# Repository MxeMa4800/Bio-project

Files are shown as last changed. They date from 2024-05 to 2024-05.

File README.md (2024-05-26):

# Stegosaurus Project
The goal of this project is to create a moving robot by controlling it with a Central Pattern Generator (CPG) and virtual hormones, which simulate how the nervous system works in living things. To guarantee the robot operates realistically, the project also entails building physical models in SolidWorks and constructing electrical circuits.

## Installation 
In order to ensure a smooth start, this section includes a list of prerequisites and instructions for installing the required hardware and software for the robot project.

### **Prerequisites**

1. Operating System 
   - Windows

      
      

2. Software 
- Arduino IDE (for programming Arduino)

   
   
   

- SolidWorks (for robot design)

    
   
   

 3. Hardware

      <table style="width:100%; border-collapse: collapse;">
      <thead>
         <tr>
            <th style= "text-align:center;">No.</th>
            <th style= "text-align:center;">List</th>
            <th style= "text-align:center;">Image</th>
            <th style= "text-align:center;">Amount (Pcs)</th>
         </tr>
      </thead>
      <tbody>
         <tr>
            <td style= "text-align:center;">1.</td>
            <td style= "text-align:center;">Arduino UNO R4 WIFI</td>
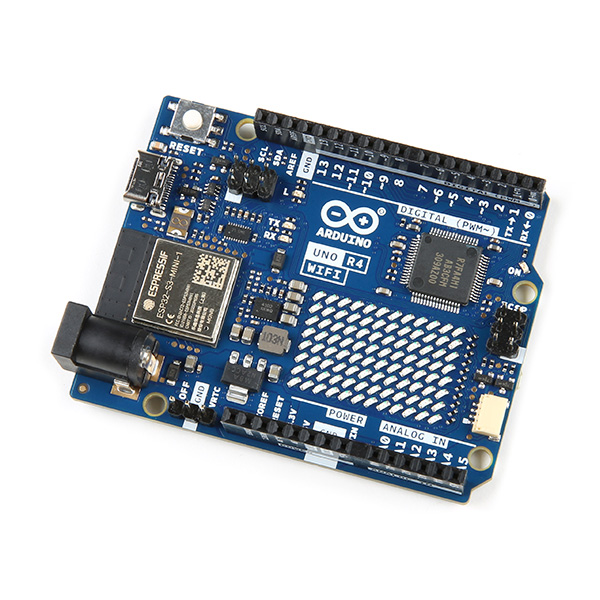
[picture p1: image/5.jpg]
            <td style= "text-align:center;"></td>
            <td style= "text-align:center;">1</td>
         </tr>
         <tr>
            <td style= "text-align:center;">2.</td>
            <td style= "text-align:center;">FE-URT-1</td>
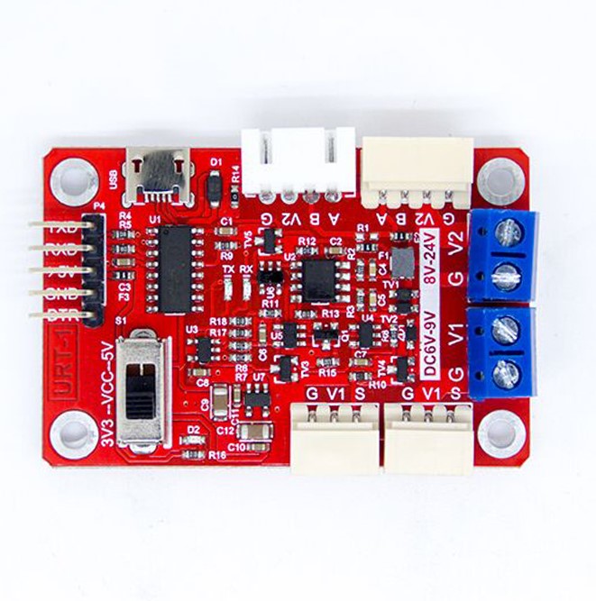
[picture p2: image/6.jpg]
            <td style= "text-align:center;"></td>
            <td style= "text-align:center;">1</td>
         </tr>
         <tr>
            <td style= "text-align:center;">3.</td>
            <td style= "text-align:center;">SCS15</td>
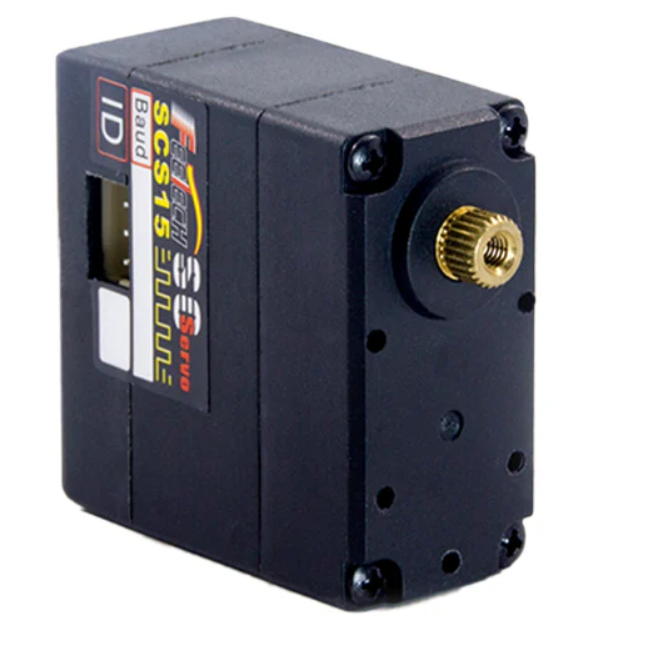
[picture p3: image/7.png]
             <td style= "text-align:center;"></td>
            <td style= "text-align:center;">8</td>
         </tr>
         </tr>
            <td style= "text-align:center;">4.</td>
            <td style= "text-align:center;">Helicox 3000mA</td>
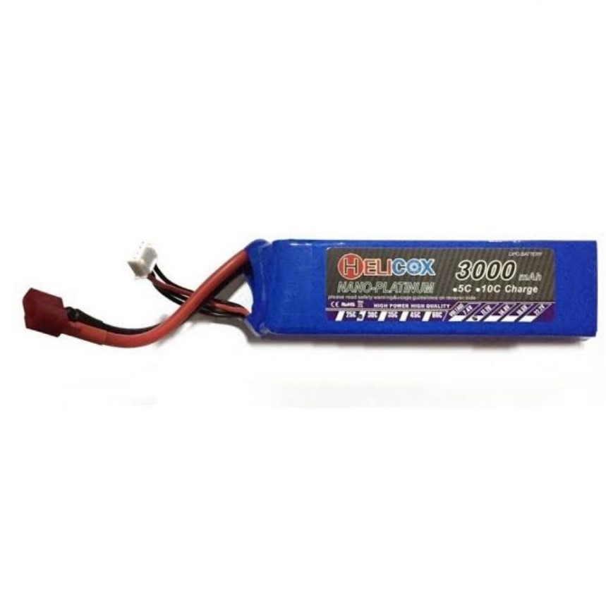
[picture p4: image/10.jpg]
             <td style= "text-align:center;"></td>
            <td style= "text-align:center;"> 1 </td>
         </tr>
         </tr>
            <td style= "text-align:center;">5.</td>
            <td style= "text-align:center;">US-015 Ultrasonic Sensor Module</td>
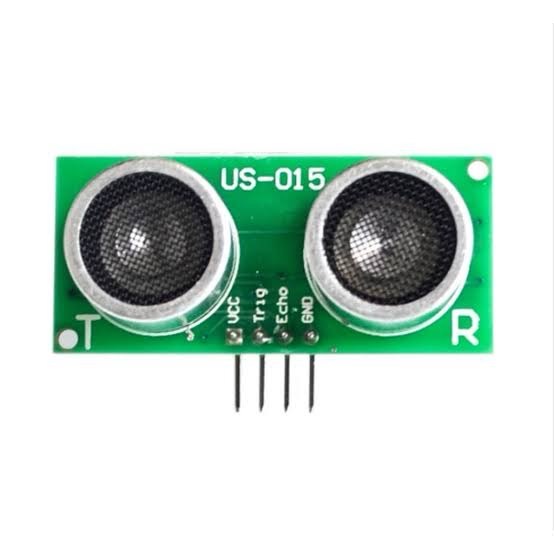
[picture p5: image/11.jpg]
             <td style= "text-align:center;"></td>
            <td style= "text-align:center;"> 2 </td>
         </tr>
          </tr>
            <td style= "text-align:center;">6.</td>
            <td style= "text-align:center;">Vehicle tires</td>
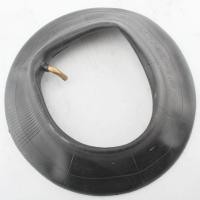
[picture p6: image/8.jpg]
             <td style= "text-align:center;"></td>
            <td style= "text-align:center;"> 1 </td>
         </tr>
      </tbody>
      </table>

### **Software Installation Steps**
1. Install Arduino IDE
- The Arduino IDE can be downloaded and installed from the [Arduino website](https://www.arduino.cc/en/software/).
- Launch the Arduino IDE and add the required libraries, like Math and [SCServo](https://github.com/IS2511/SCServo/blob/master/SCSCL.cpp). 
   
   **Zip file installation for the library**
   - Get the Library from here in a zip file. 

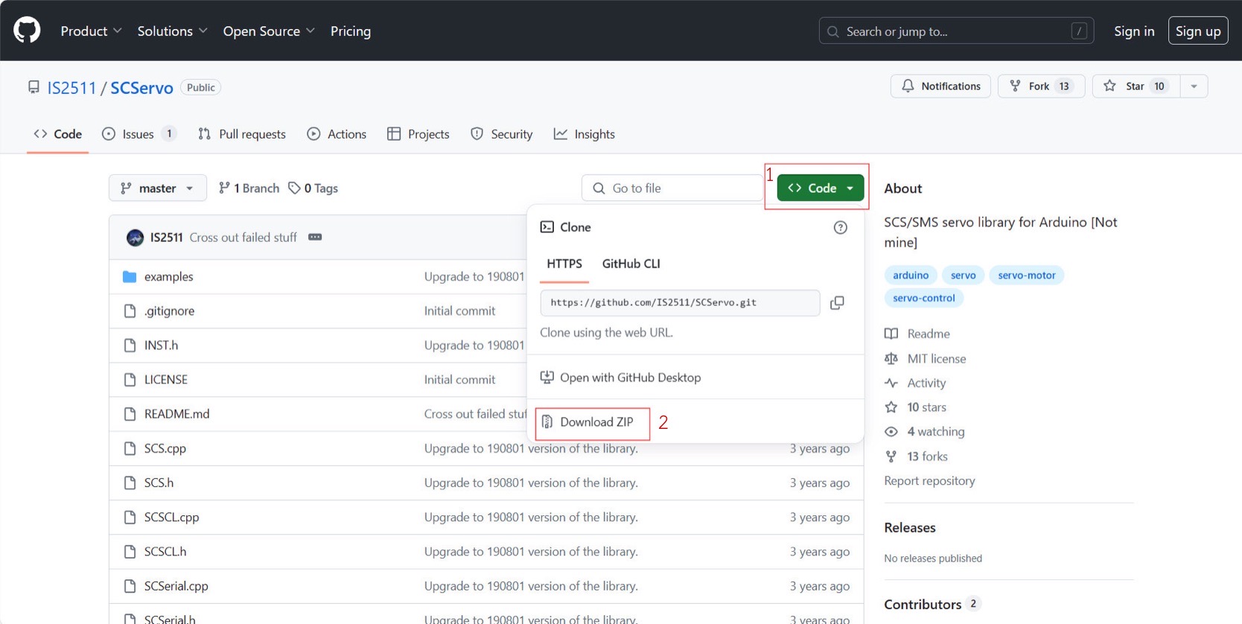
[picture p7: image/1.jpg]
      

   - Open the Arduino IDE program, go to Sketch > Include Library > Add .ZIP Library, then pick the file that you downloaded.

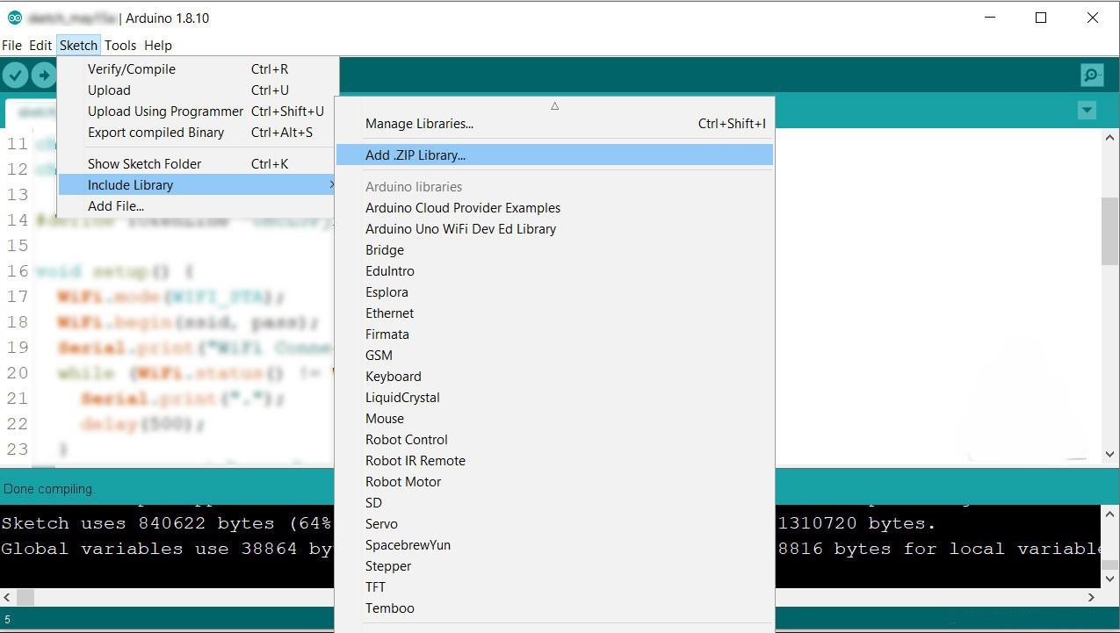
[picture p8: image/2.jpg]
      

    **Installing more Arduino libraries**

     - Open the Arduino IDE program, go to Sketch > Include Library > Manage Libraries.
     
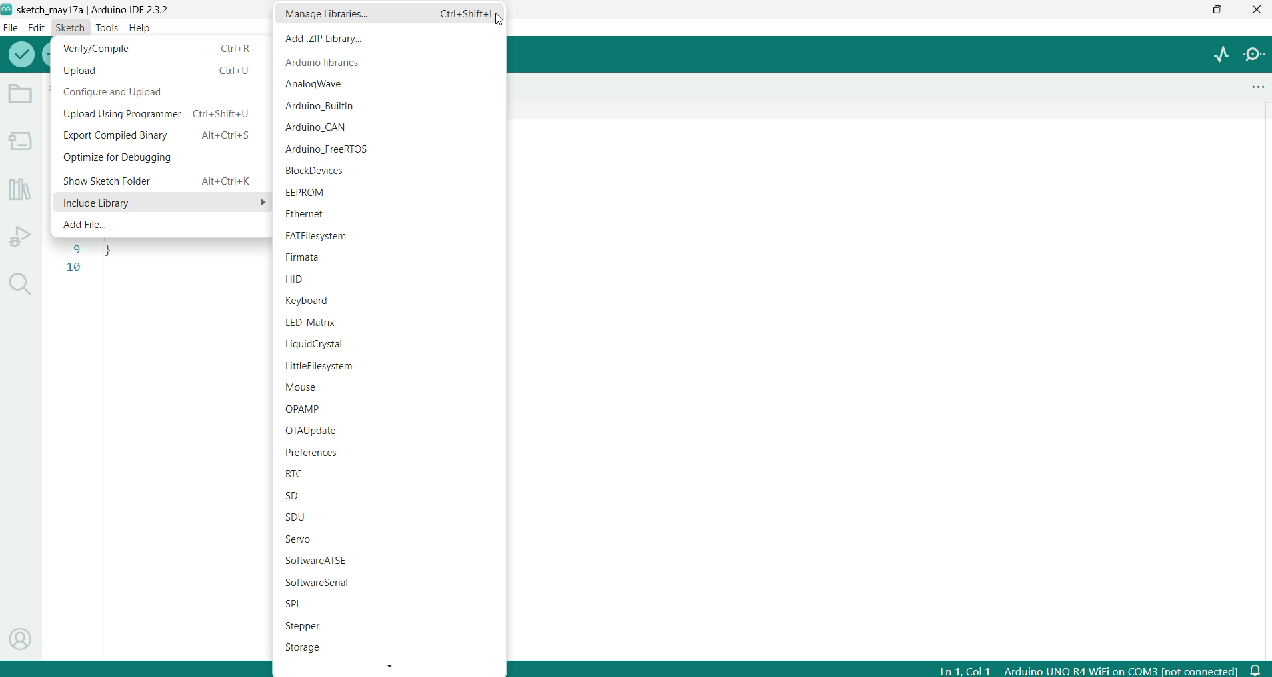
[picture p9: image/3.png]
        

    - In the search box, type the name of the desired library. Click More info to see how to utilize it. Click the Install button in order to install.
      
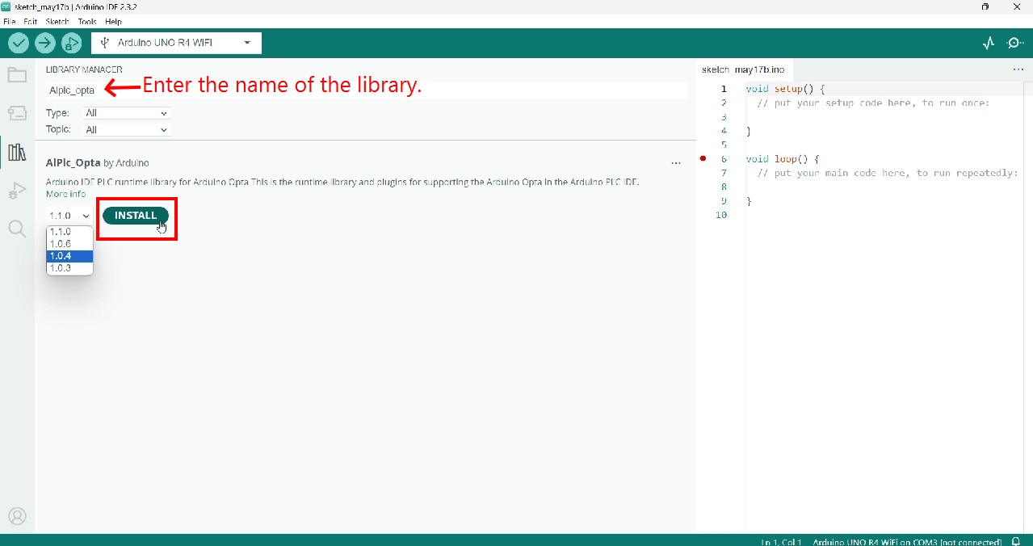
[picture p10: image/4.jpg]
      

2. Install SolidWorks
- SolidWorks can be downloaded and installed from the [SolidWorks official website](https://www.solidworks.com/sw/support/downloads.htm).
- Launch SolidWorks and confirm that all required modules, including Part, Simulation and Electrical, are installed.

### **Hardware Installation Steps**
1. Assemble the Robot Structure
- The robot's primary structure can be constructed using the assembly guide found in the SolidWorks files.
- Place electrical in the designated locations.   
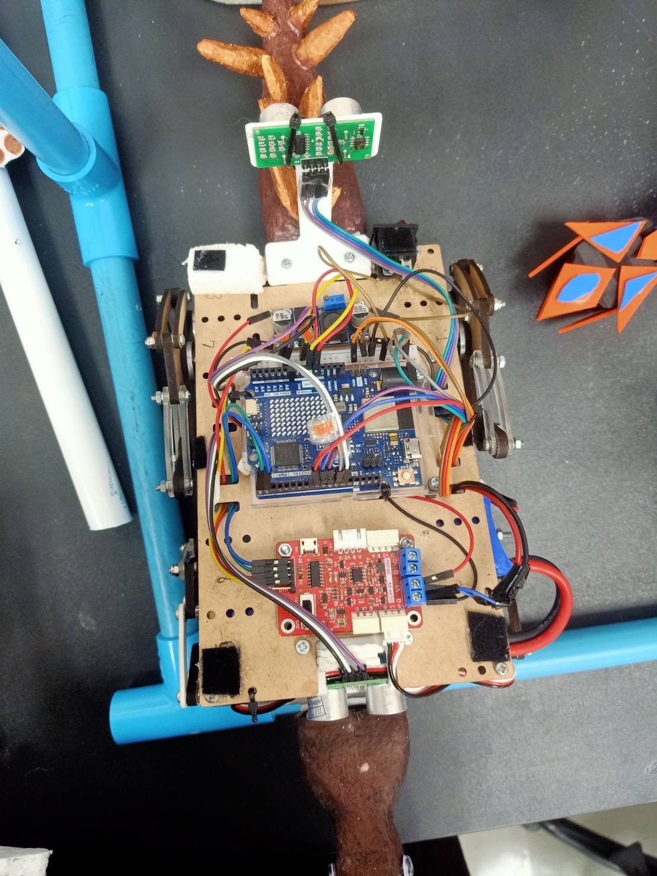
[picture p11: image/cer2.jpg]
   
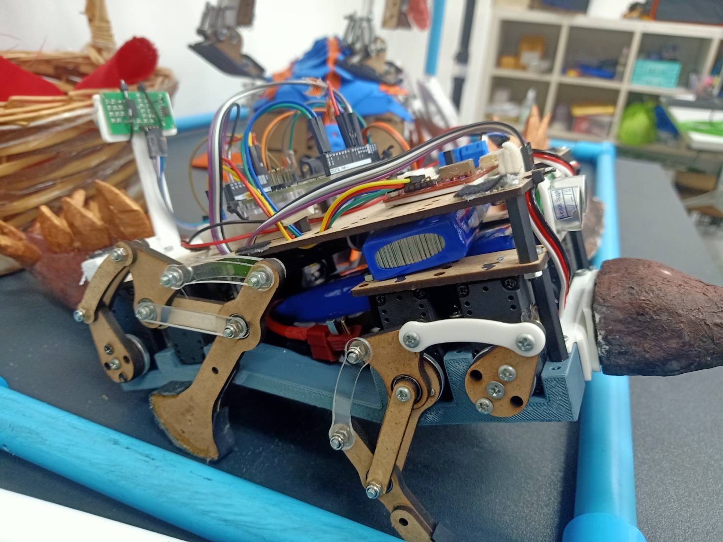
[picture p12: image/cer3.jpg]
   
2. Connect the Electrical Circuit

- Wires between the microcontroller(Arduino uno r4), servo, sensors, and batteries should be installed and connected using the electrical circuit schematic.
- Make sure every connection is safe and secure.

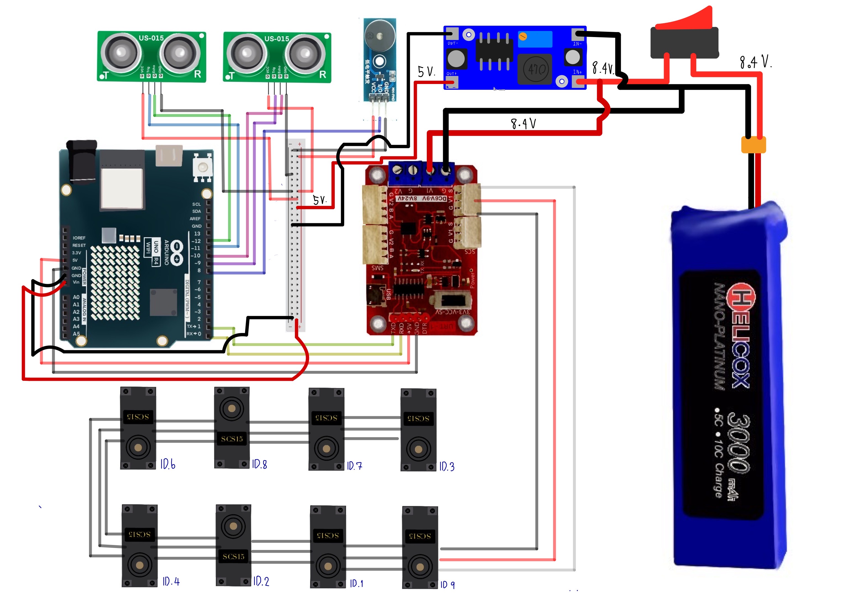
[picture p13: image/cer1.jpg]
   

3. Energy consumption
   - The battery used is a Helicox 3000mA. A single battery can last approximately 1-2 hours,    as can be seen from the following calculations
     
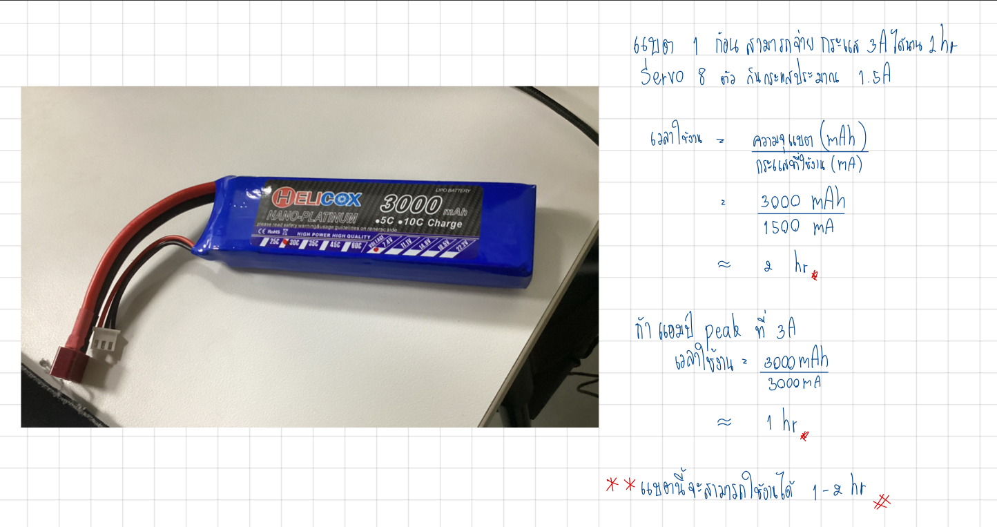
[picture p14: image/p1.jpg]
     
## Robot Design
### **Main Structure**
1. This robot is designed to walk on four legs, with the main materials used being: 

   - PLA+ Filament 

   - Acrylic 2 mm thick 

   - Wooden boards 2.5 mm and 4 mm
     
   ** Replacing the leg material from wood to acrylic might yield better results, but be cautious of material breakage.
   
   Assemble whit out skin
   
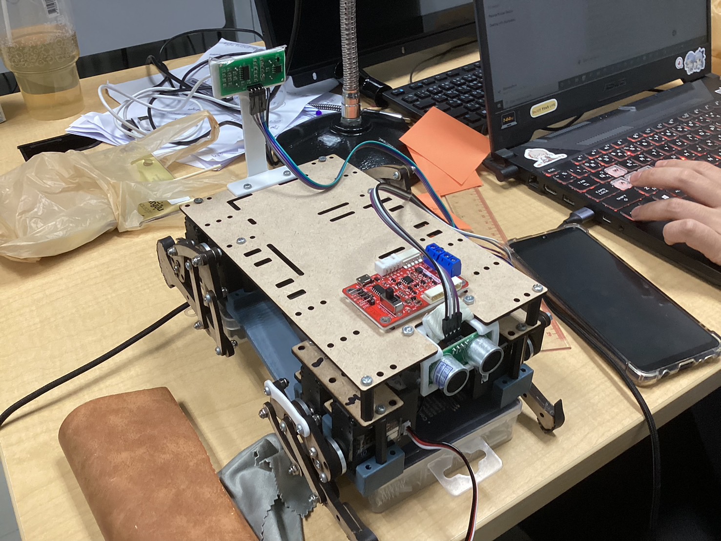
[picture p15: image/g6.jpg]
   
   
   Assemble full skin
   
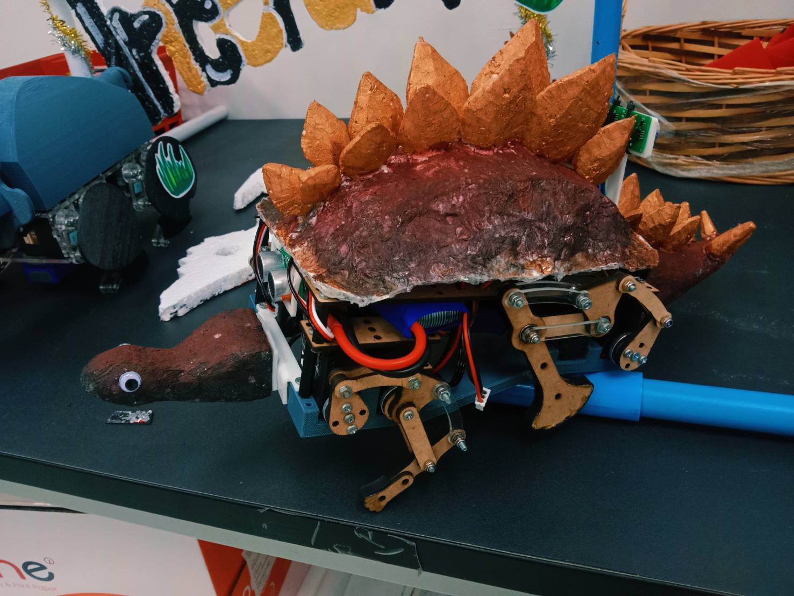
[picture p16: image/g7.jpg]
   

 3. The skeleton of the Stegosaurus has front and hind legs of different sizes. Therefore, the designer made the front and hind legs of different sizes, with a ratio of 1:1.51, but the size difference does not exceed 2 times.
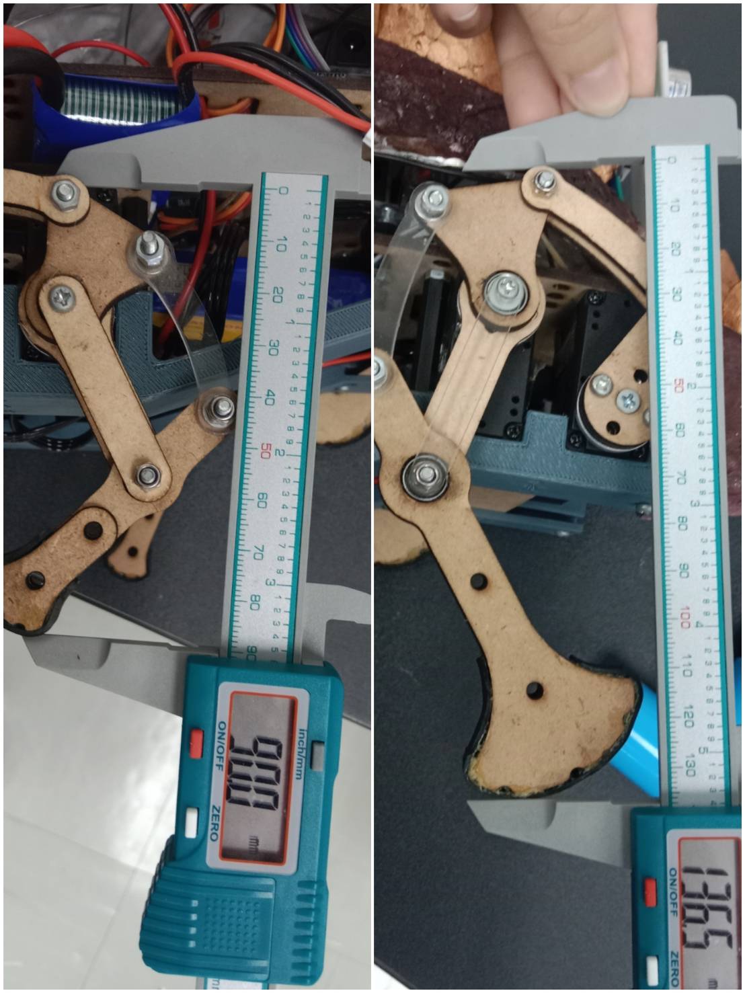
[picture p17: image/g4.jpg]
   
   
 3.Based on calculations, this robot can support a weight of approximately 1500 grams, with a tolerance of ±250 grams

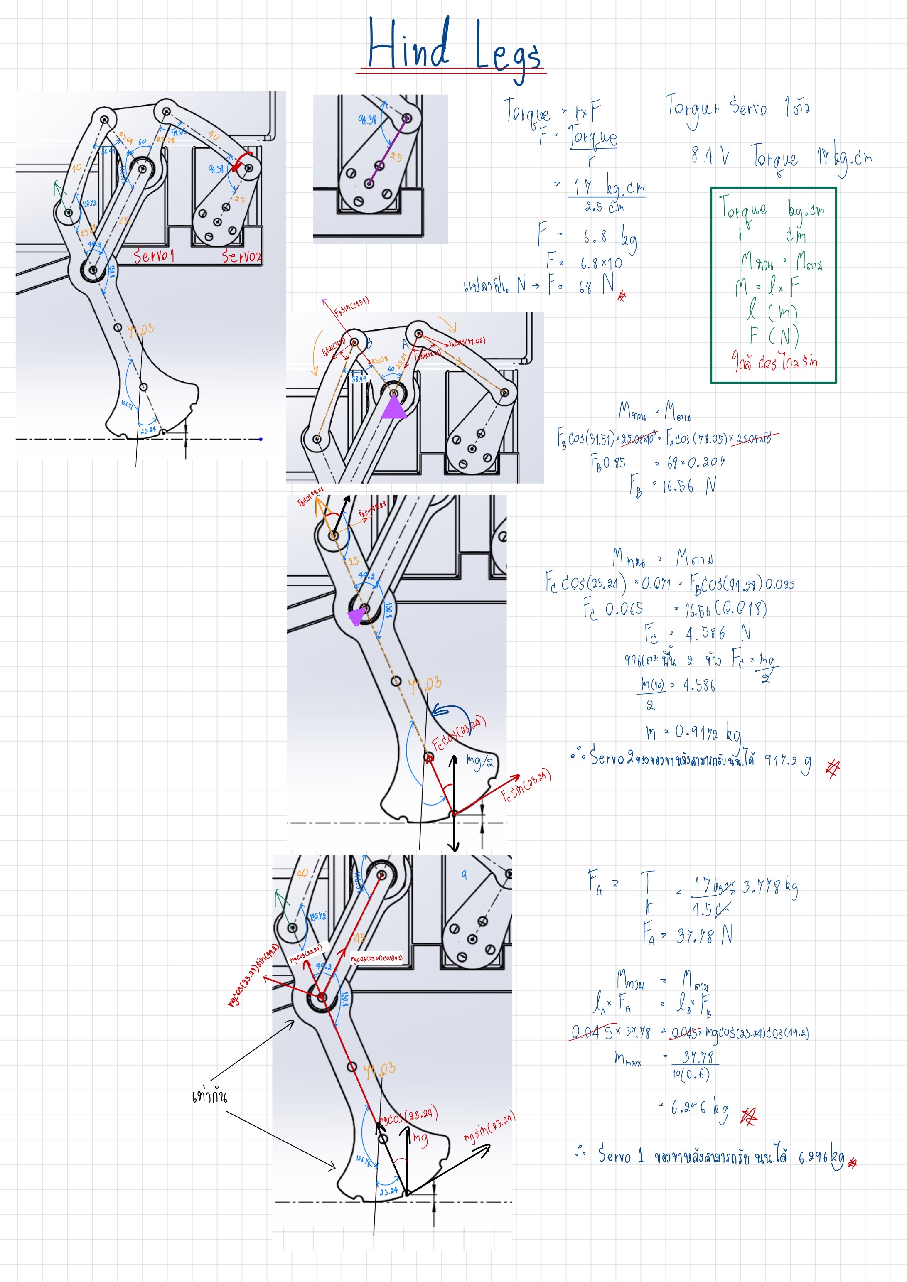
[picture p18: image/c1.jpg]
   
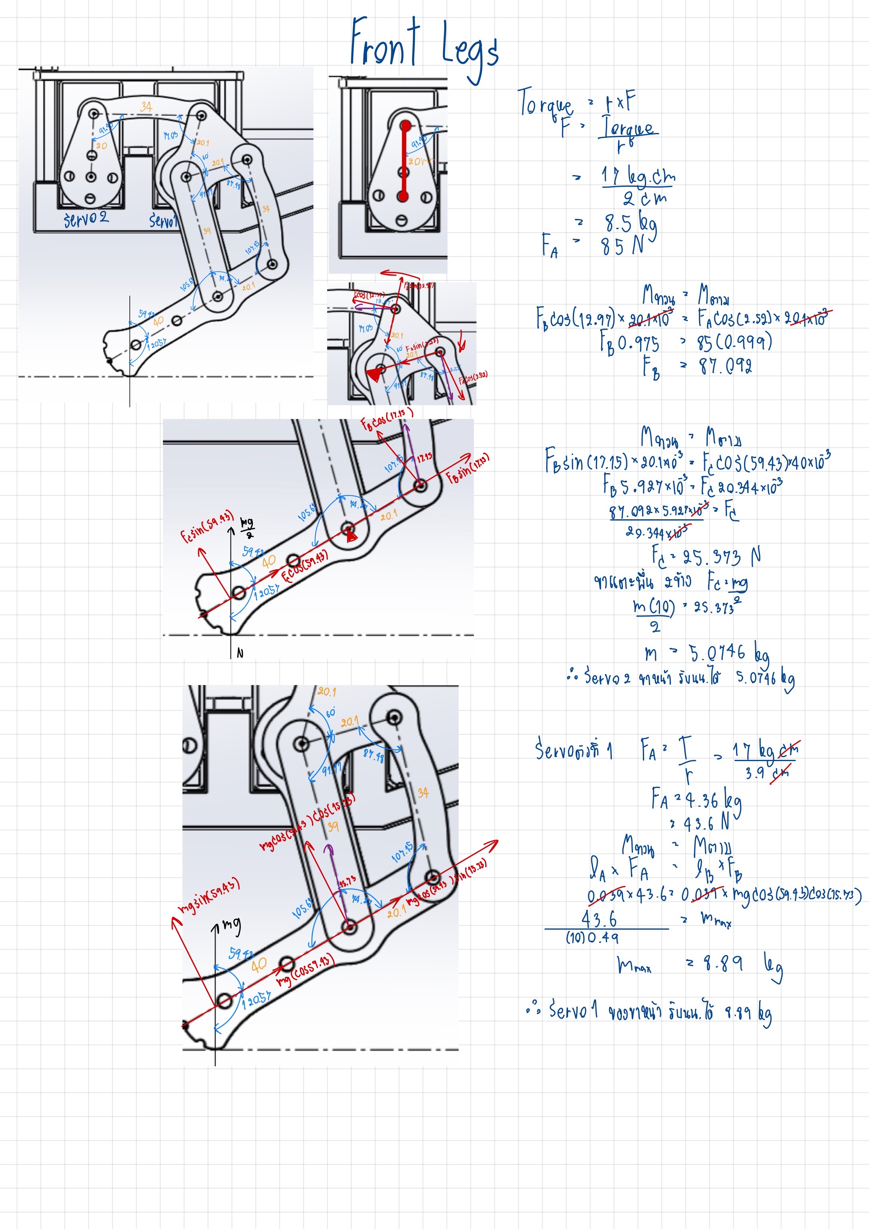
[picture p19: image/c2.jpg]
   
 4. The designer tested and found that the hind legs can support a weight of 750 grams. When the robot starts walking, there are always two legs on the ground. Therefore, the robot can support a weight of approximately 1500 grams, with a tolerance of no more than ±250 grams.
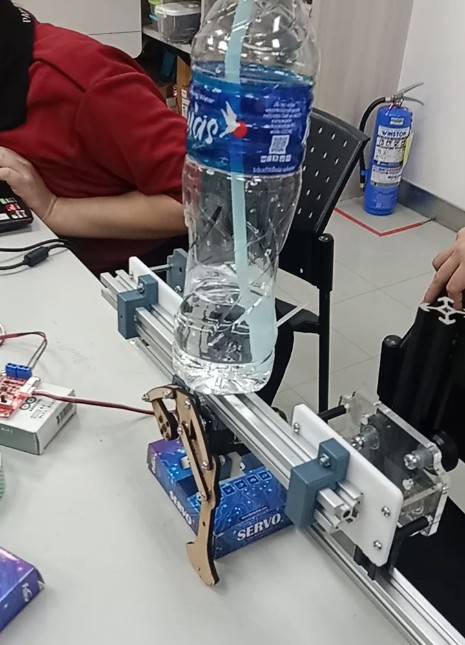
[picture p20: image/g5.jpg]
   
 5. You can view the CAD model in the STEP file named as shown in the image.
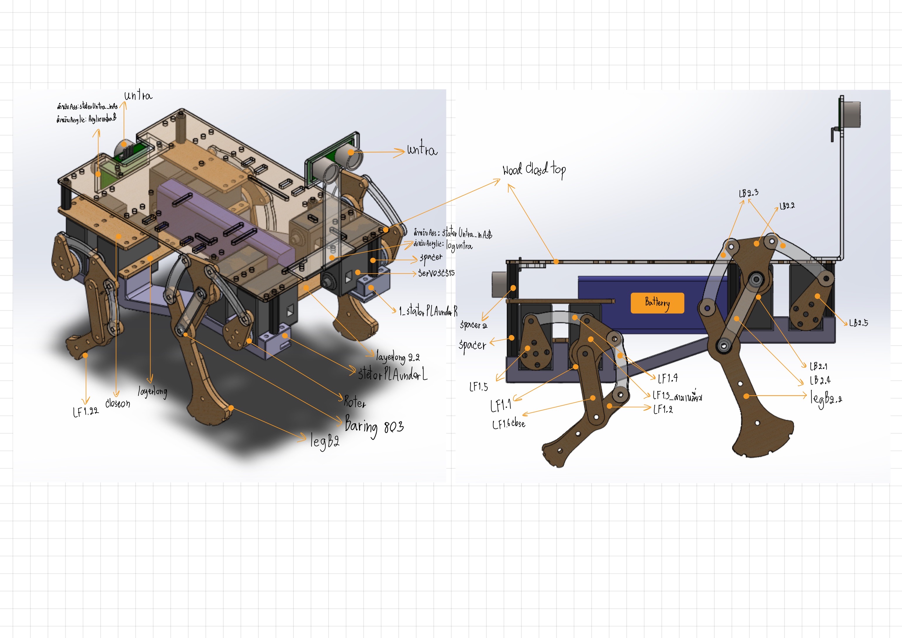
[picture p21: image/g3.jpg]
    

### **Joints and Actuators**

- The robot has wood for its joints and legs. To further aid secure the armor to the ground, rubber was also used to protect the feet.

   [Watch the video on YouTube](https://youtu.be/n-jgDqc_dPE)

## Configuration and Customization
1. CPG 

   Utilize the values for O1 and O2 to run the motor. To move the legs up and down, use O2, and to go forward and backward, use O1.

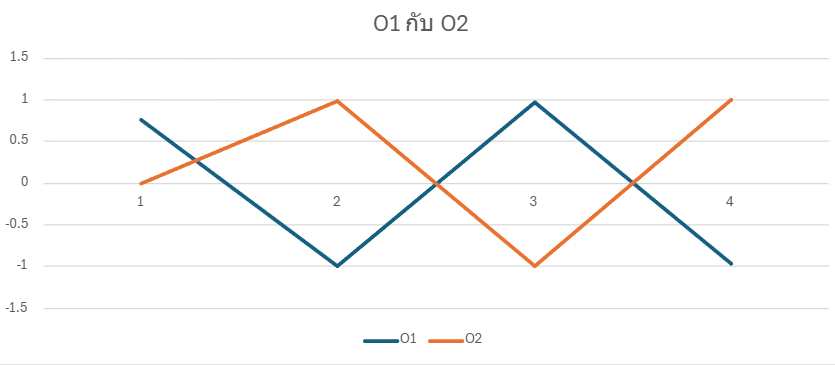
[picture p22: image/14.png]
    
   
      Values for O1 and O2, derived from graphing in [excel](https://pim365-my.sharepoint.com/:x:/r/personal/6452500121_stu_pim_ac_th/_layouts/15/Doc.aspx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)

2. Hormones Concentration(HC)

   Takes the value of the sensor as input. Then take the standard deviation to represent the hormonal changes in each period. Then bring it into the hormone equation to get the amount of hormones secreted, which is the HC value.In addition, the HC value must be calculated with the Hormones Receoter to get the value that affects mood.
   
   You can find about Hormone calculation from [here](https://docs.google.com/spreadsheets/d/1ysU-uzWMpW0UrVVLxHHKWWODgd5BCDr7dVBZ5aWzhAU/edit?usp=sharing)
   
   **Graph of Hormones Concentration**

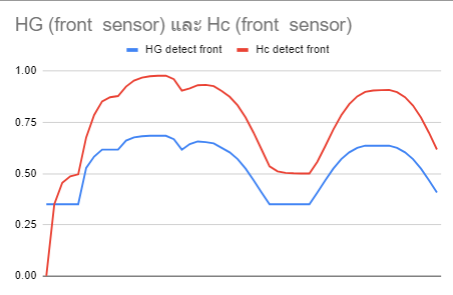
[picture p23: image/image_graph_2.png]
   
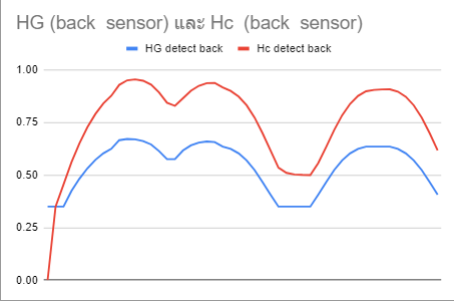
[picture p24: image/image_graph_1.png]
   

   _For adjusting alpha and beta values. Alpha value and beta value Must be greater than 0 and not more than 1.
If the beta value is close to 0, it will be close to the alpha value. and will be less similar if the beta value close to 1_

   **Hormones Gland and Receptor**

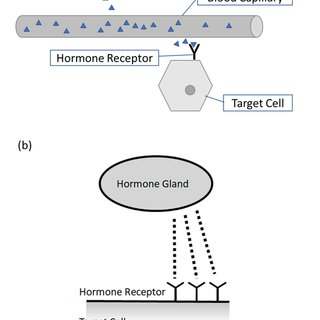
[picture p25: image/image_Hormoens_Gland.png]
   

   **Condition value without Hormone and value with Hormone**
   
   The difference between having and not having hormones will result in a change in the behavior of the robot. This is because the changing hormonal values affect the conditions in which the robot responds.

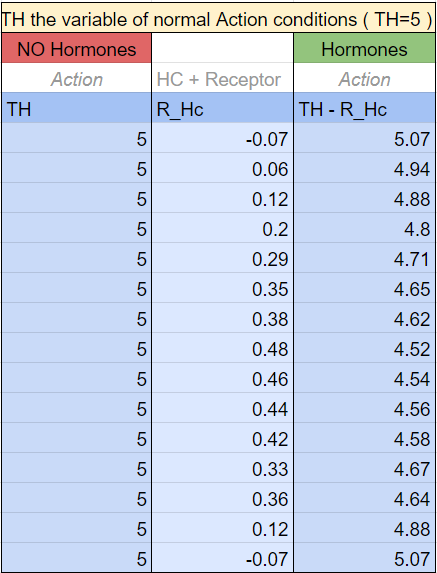
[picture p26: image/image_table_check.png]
   
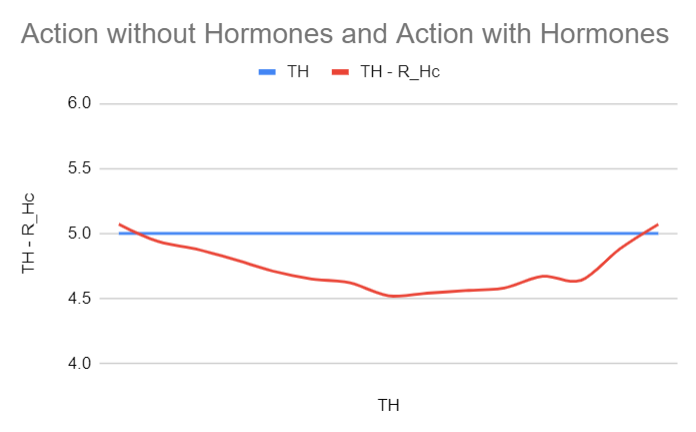
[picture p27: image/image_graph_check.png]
   

   _The blue lines indicate the values that are the operating conditions for the robot. That's different from the red line where hormones are part of the variables that affect working conditions. The range of values used to actuate will vary according to the hormone levels in the robot._
   
   **Graph of Action without Hormone and Action with Hormones**
   
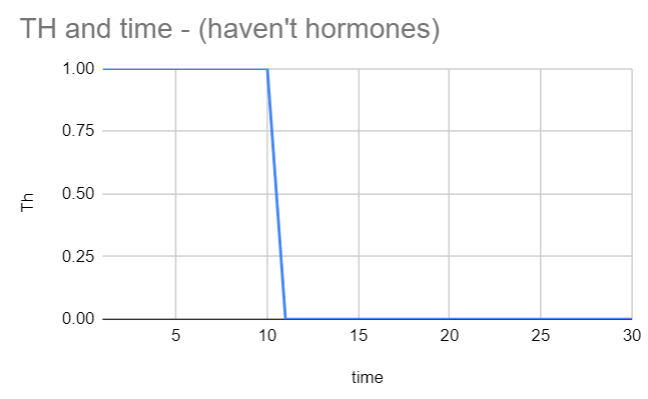
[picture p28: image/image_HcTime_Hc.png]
   
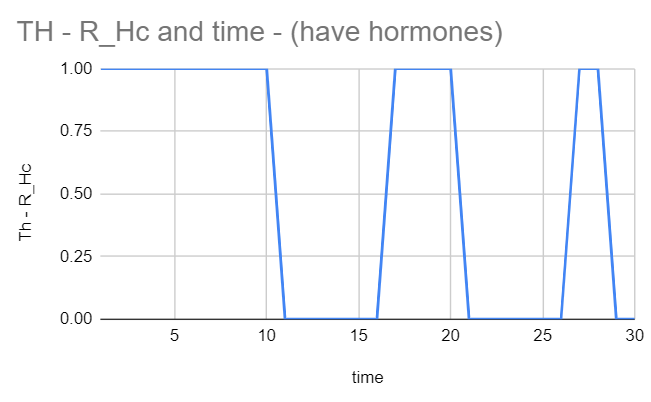
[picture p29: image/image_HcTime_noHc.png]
   
   
   _By replacing moving with 1 and not moving as 0. It can be seen that movement under normal conditions will not change. But if there are hormones, the condition will change over time. Therefore, walking occurs when hormonal stress of fear subsides._   
   
4. Walking Test Steps
   - Experiment 1:  
         - In this experiment, we will conduct walking tests on two types of terrain: flat             terrain without obstacles and flat terrain with obstacles. 
         - Additionally, we will compare the effectiveness of walking with and without                 springs. Which method is more effective?
         - by having the robot walk a distance of 50 centimeters within 15 minutes.
     
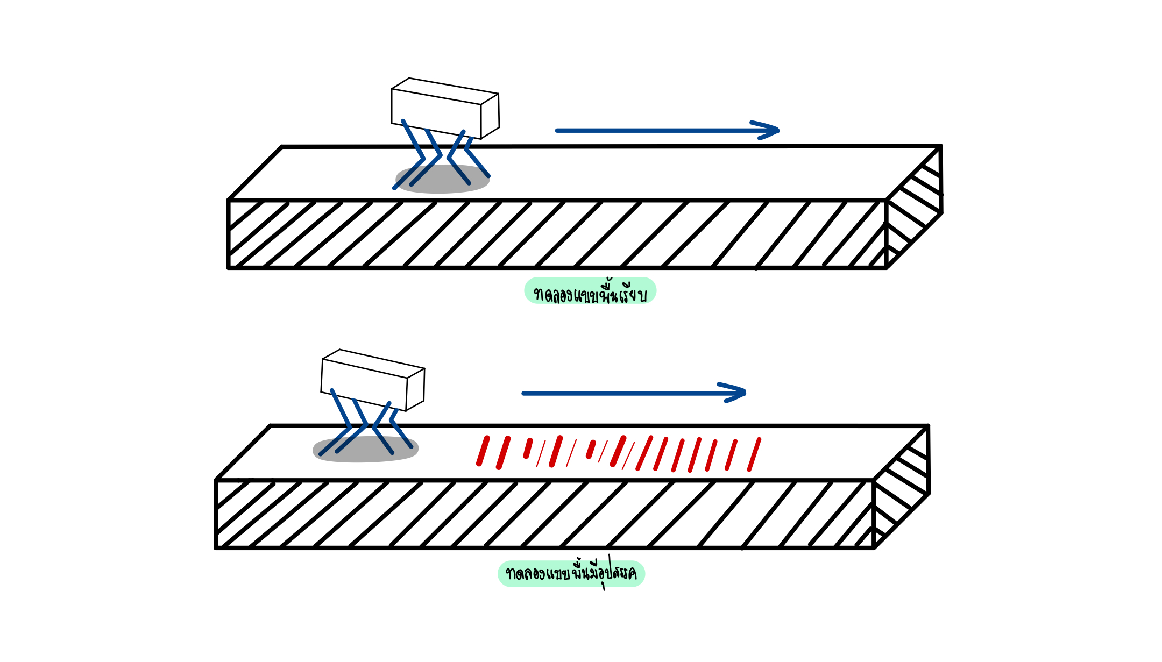
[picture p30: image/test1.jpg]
     

   - You can watch a video clip for the experiment at this link, which is a compilation of 1 video from the 4 experiments.
     [Watch the video on YouTube](https://youtu.be/K6Rzk2AfT0k)

   - From the experiment results, we summarized the findings in a graph. It was found that    walking with springs improved performance compared to walking without springs, on both obstacle-free and obstacle-laden terrain. However, for the walking test on obstacle-laden terrain without springs, we could not conclude the results in the last three trials because the robot front legs broke.
     
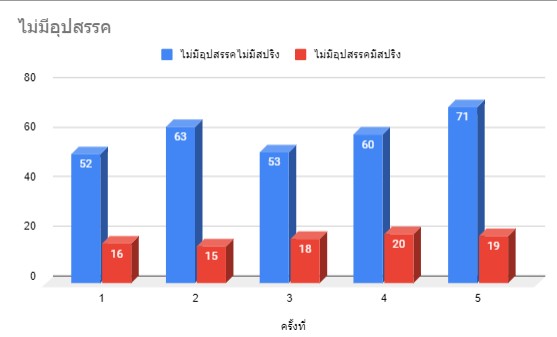
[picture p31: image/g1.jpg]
     
        No Obstacle Blue color = With spring, Red color = Without spring
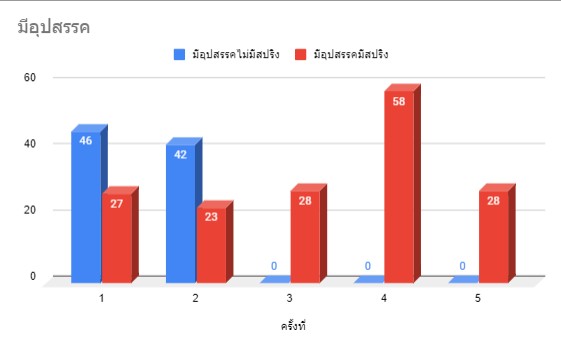
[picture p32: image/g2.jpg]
     
        Obstacle Blue color = With spring, Red color = Without spring
        
      - X-axis = Seconds, Y-axis = Number of occurrences

## Authors and Contributors
- Miss Supannee   Saengwonrarach    6452500121
- Miss Phansa     Romruen           6452500155
- Miss Awanta     Arwon             6452500236
- Miss Thanita    Kaeoking          6452500244
- Miss Napasawan  Sittikham         6452500295
- Miss Sudaporn   Saenyakiattikhun  6452500376

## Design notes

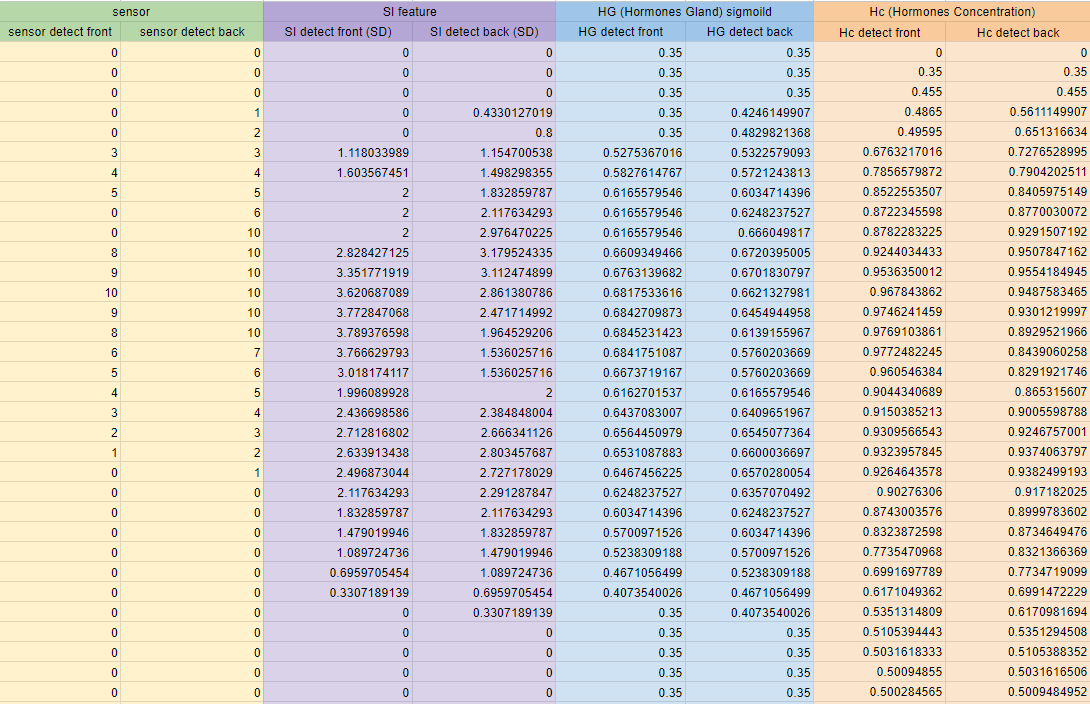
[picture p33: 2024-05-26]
image/image_table_Hc.png

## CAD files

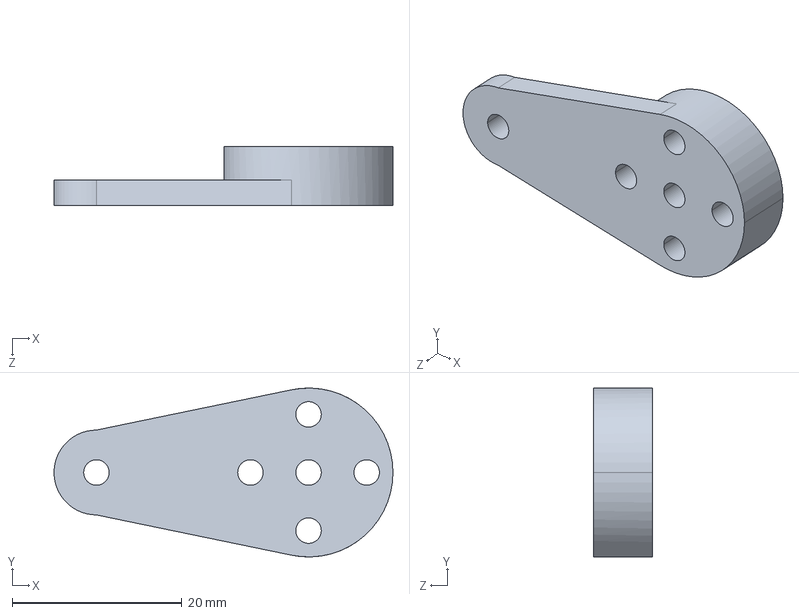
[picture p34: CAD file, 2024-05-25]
step/LB2.5.STEP
40.0 x 19.9 x 7.00 mm

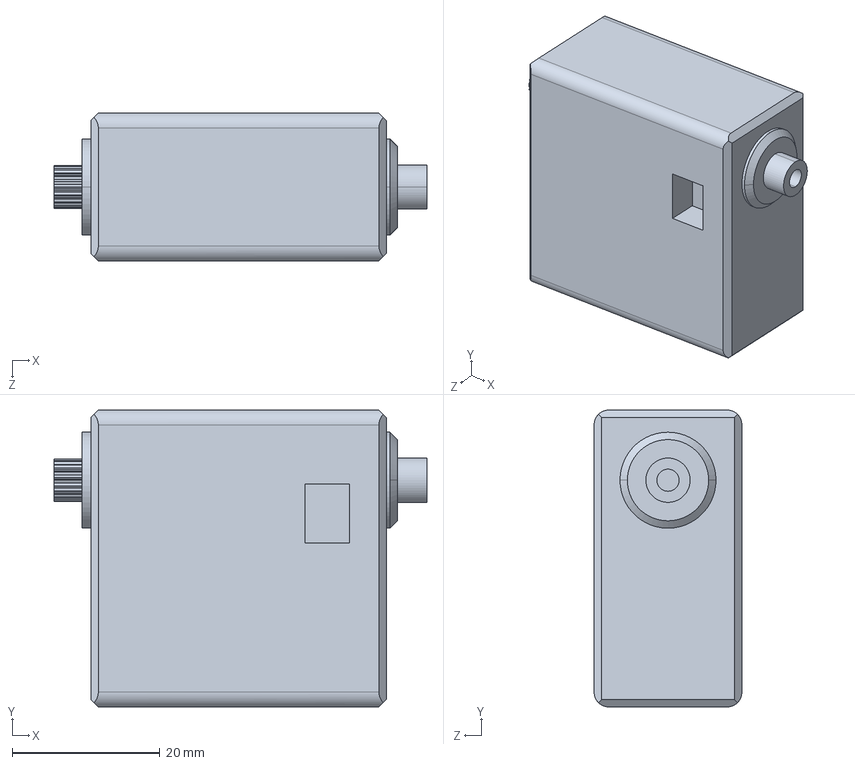
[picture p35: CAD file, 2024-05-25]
step/servoscs15.STEP
50.5 x 40.2 x 20.0 mm

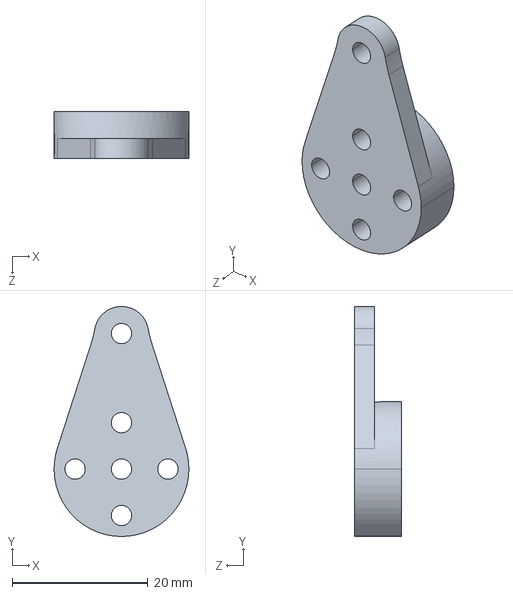
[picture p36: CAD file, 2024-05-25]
step/LF1.5.STEP
19.9 x 33.9 x 7.00 mm

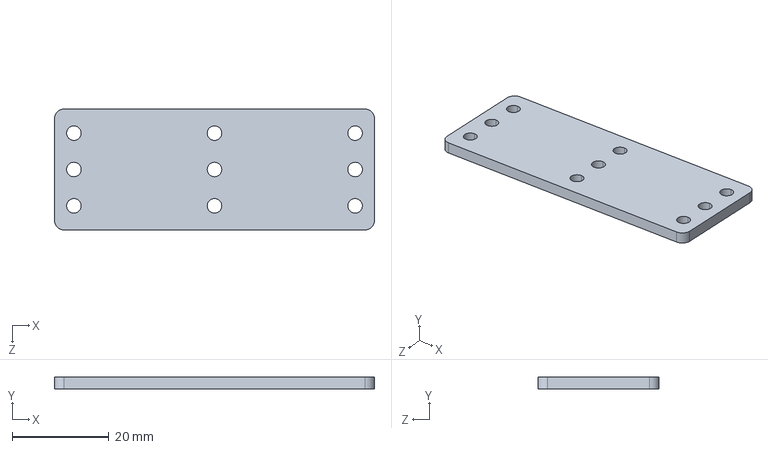
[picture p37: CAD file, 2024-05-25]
step/closeon.STEP
66.0 x 2.50 x 25.0 mm

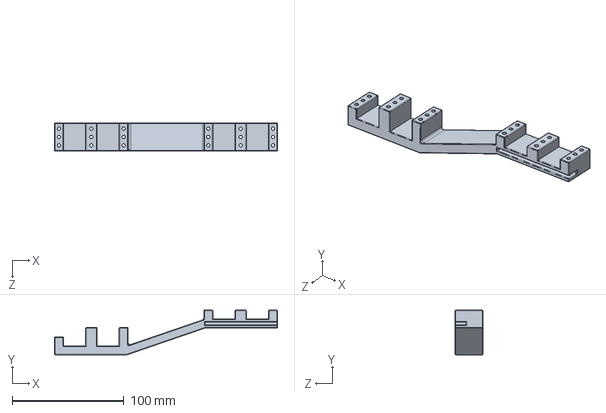
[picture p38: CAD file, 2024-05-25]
step/1_statorPLAunderR.STEP
200.0 x 40.0 x 25.0 mm

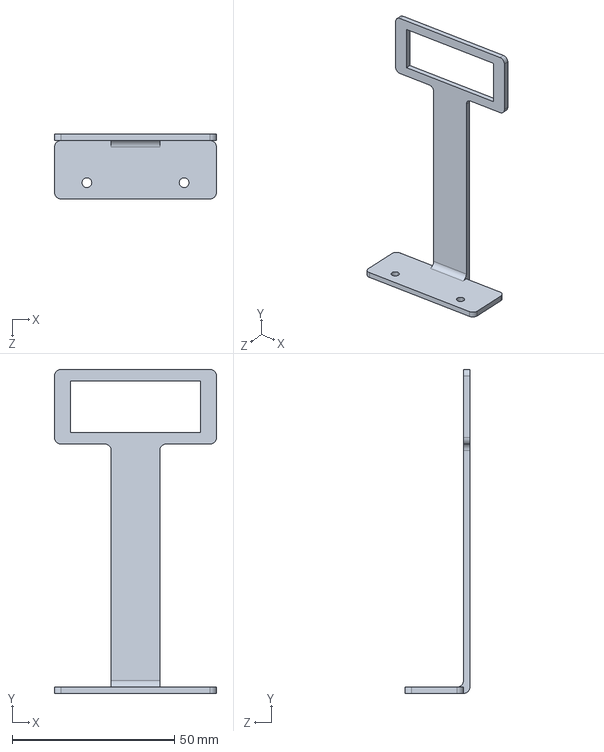
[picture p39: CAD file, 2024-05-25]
step/staterUntra_inAsB.STEP
50.0 x 100.0 x 20.0 mm

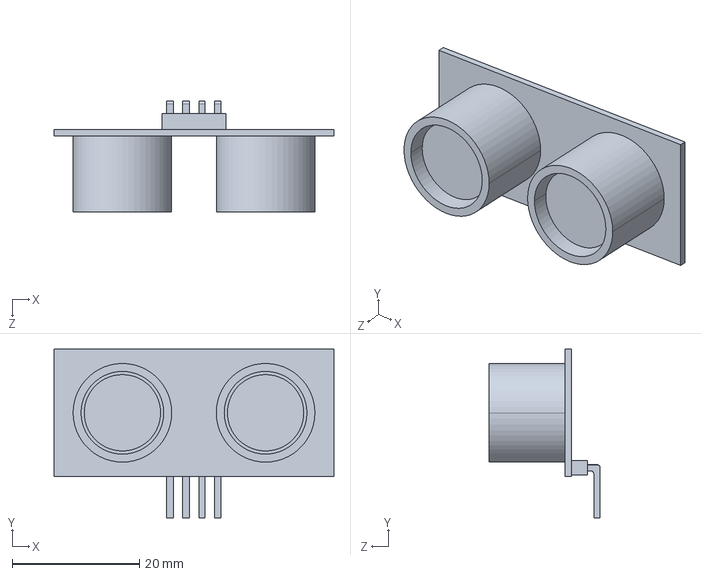
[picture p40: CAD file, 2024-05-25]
step/untra.STEP
44.0 x 26.5 x 17.5 mm

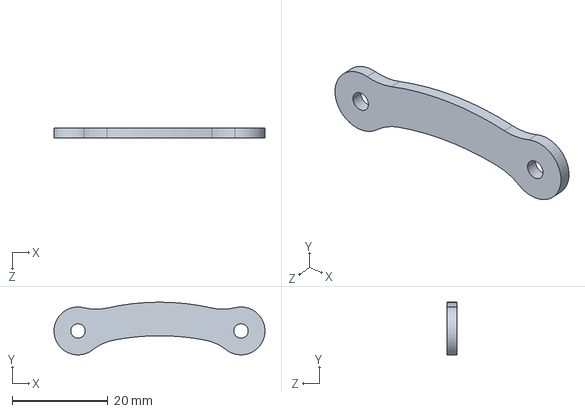
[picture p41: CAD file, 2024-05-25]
step/LF1.4.STEP
44.0 x 11.0 x 2.00 mm

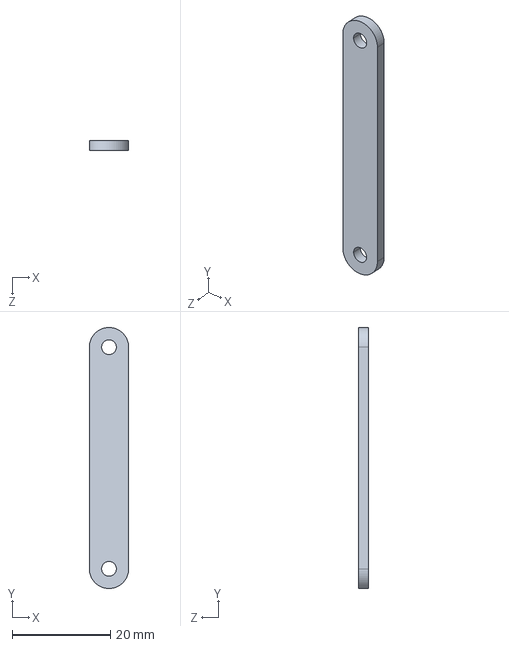
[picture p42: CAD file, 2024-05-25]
step/LB2.4.STEP
8.00 x 53.0 x 2.00 mm

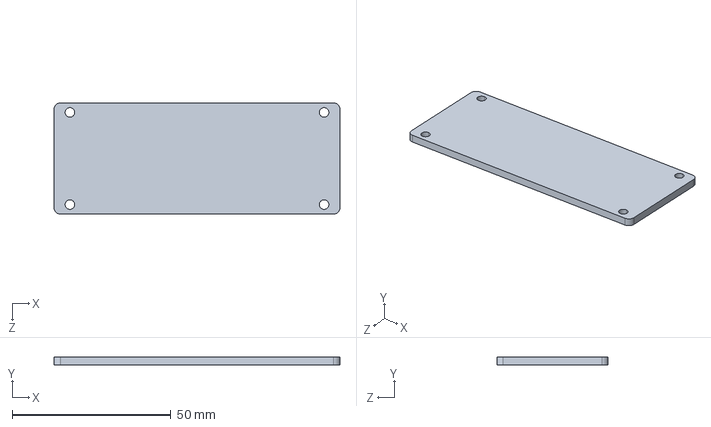
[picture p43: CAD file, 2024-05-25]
step/layerlong2.2.STEP
90.0 x 2.50 x 35.0 mm

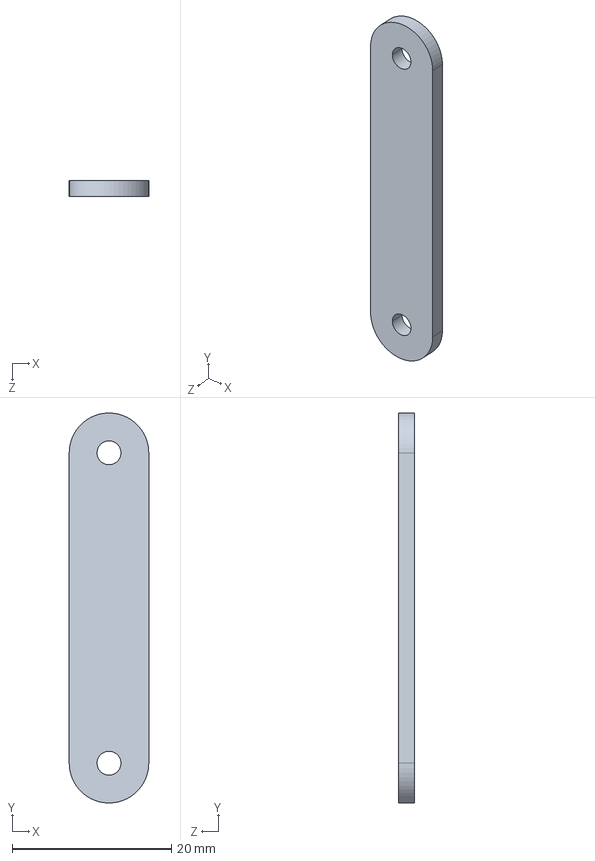
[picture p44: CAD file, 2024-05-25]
step/LF1.6close.STEP
10.0 x 49.0 x 2.00 mm

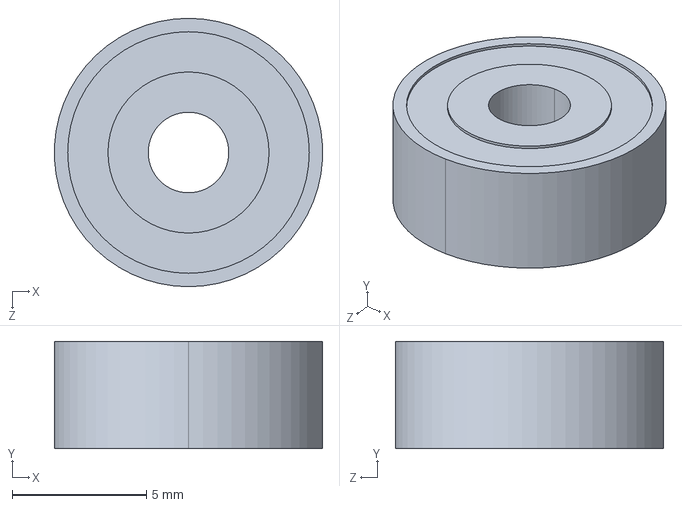
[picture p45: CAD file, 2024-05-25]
step/Baring.STEP
9.99 x 4.00 x 10.0 mm

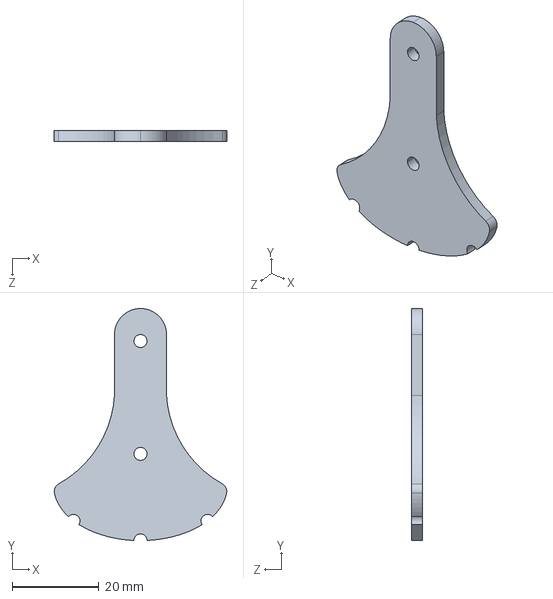
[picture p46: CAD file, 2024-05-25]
step/legB2.STEP
39.8 x 53.5 x 2.50 mm

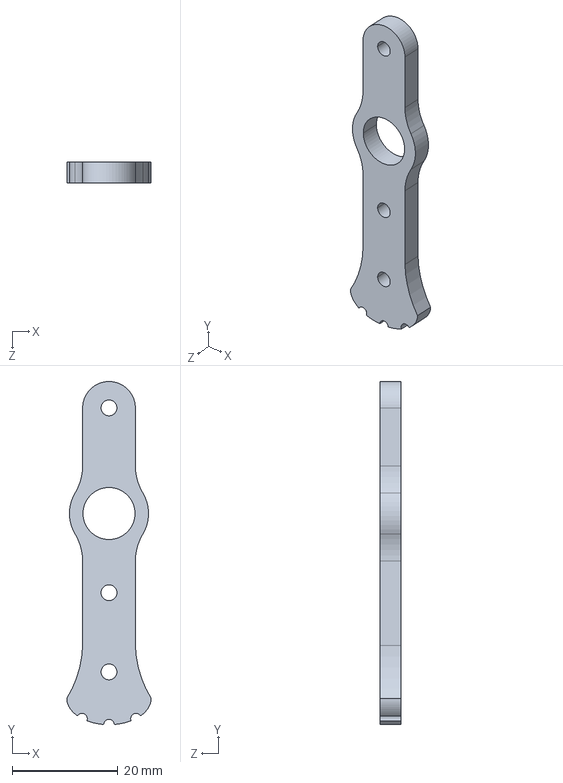
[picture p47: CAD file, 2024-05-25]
step/LF1.2.STEP
16.0 x 65.0 x 4.00 mm

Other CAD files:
step/statorPLAunderL.STEP
step/LB2.1.STEP
step/staterUntra_inAs.STEP
step/batterry.STEP
step/LB2.2.STEP
step/LB2.3.STEP
step/LF1.1.STEP
step/LF1.22.STEP
step/LF1.3_สามเหลี่ยม.STEP
step/Rotor.STEP
step/acylicuntraB.STEP
step/layerlong.STEP
step/legB2.2.STEP
step/loguntra.STEP
step/spacer.STEP
step/spacer2.STEP
step/woodClosdtop.STEP

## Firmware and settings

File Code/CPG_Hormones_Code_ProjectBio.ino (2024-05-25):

#include <math.h>  // Include the math library for sqrt()
#include <SCServo.h>
SCSCL sc;

/// ------- CPG ---------///
unsigned long previousMillis4 = 0;
const long interval4 = 400; // interval at which to update (milliseconds)
int j = 0; // move the loop variable to global scope

unsigned long previousMillis3 = 0;
const long interval3 = 400;

const int Output = 5;
float C1_Values[Output];
float C2_Values[Output];
float O1_Values[Output];
float O2_Values[Output];

float C1 = 1;
float C2 = 1;
float O1;
float O2;
float W11, W12, W21, W22;
float alpha = 6;
float phi = 2.6;
int i = 0;  //time


//จุดต่ำสุดสูงสุดของกราฟ O1
float MIN_O1 = -0.999206032;
float MAX_O1 = 0.970415895;

//จุดต่ำสุดสูงสุดของกราฟ O2
float MIN_O2 = -0.99999983;
float MAX_O2 = 0.999999831;

// //----------เดินหน้า---------------//
//ขาหน้าขวา
const int MAX_ID6 = 662;  //ยกขาขึ้น
const int MIN_ID6 = 562;  //ยกขาลง 562
const int MAX_ID8 = 301;  //ก้าวขาถอย   
const int MIN_ID8 = 207;  //ก้าวขาหน้า   

//ขาหน้าซ้าย
const int MIN_ID4 = 454;  //ยกขาขึ้น 
const int MAX_ID4 = 254;  //ยกขาลง  
const int MIN_ID2 = 567;  //ก้าวขาถอย 
const int MAX_ID2 = 661;  //ก้าวขาหน้า 

//ขาหลังขวา
const int MAX_ID7 = 466;  //ยกขาขึ้น 
const int MIN_ID7 = 566;  //ยกขาลง
const int MAX_ID3 = 454;  //ก้าวขาหน้า
const int MIN_ID3 = 554;  //ก้าวขาถอย

//ขาหลังซ้าย
const int MAX_ID1= 619;  //ยกขาขึ้น
const int MIN_ID1 = 519;  //ยกขาลง 
const int MAX_ID9 = 447;  //ก้าวขาหน้า
const int MIN_ID9 = 347;  //ก้าวขาถอย


float map(float x, float in_min, float in_max, float out_min, float out_max) {
  return (x - in_min) * (out_max - out_min) / (in_max - in_min) + out_min;
}

bool working1 = false;
bool work1 = false;
bool doing1 = false;
bool working2 = false;
bool work2 = false;
bool doing2 = false;

/// ------- CPG ---------///

// ------ hormones variable -------- //
const int trigPin1 = 11;    // Trigger for sensor 1
const int echoPin1 = 12;    // Echo for sensor 1
const int trigPin2 = 9;     // Trigger for sensor 2
const int echoPin2 = 10;    // Echo for sensor 2

unsigned long previousMillis = 0;
const long interval = 100;  // Interval between readings in milliseconds
float duration1, cm1;
float duration2, cm2;

// Define array size
const int arraySize = 8; // Array size set to 8

// Arrays to store distance values
int sensor1Values[arraySize];
int sensor2Values[arraySize];

// Counter to track the number of valid entries in the array
int validEntries = 0;

// Index to keep track of the current position in the arrays
int index = 0;

// Array to store Hc1 values
float Hc1[2] = {0, 0};
float Hc2[2] = {0, 0};

// ------ end hormones variable -------- //

//// ----- buzzer voice ------- ////
const int buzzerPin = 8;
bool isPeeping = false;
// Define the frequency of the beep (in Hertz)
const int beepFrequency = 1000; // Adjust the frequency as needed
const int beepFrequency2 = 800;
// Define the duration for the beep (in milliseconds)
const unsigned long beepDuration = 3000; // 1 second
// Variables to manage timing
unsigned long startMillis2;
bool isBeeping = false;
bool beepCompleted = false;
//// ----- end buzzer voice ------- ////



void setup() {
  Serial.begin(115200);
  //set the digital pin as output
  pinMode(buzzerPin,OUTPUT);
  startMillis2 = millis();
  isBeeping = true;

  pinMode(trigPin1, OUTPUT);
  pinMode(echoPin1, INPUT);
  pinMode(trigPin2, OUTPUT);
  pinMode(echoPin2, INPUT);
  // Serial.begin(115200);
  Serial1.begin(1000000);
  sc.pSerial = &Serial1;

  //------cpg----------------//
  W11 = alpha * cos(phi);
  W12 = alpha * sin(phi);
  W21 = alpha * (-sin(phi));
  W22 = alpha * cos(phi);


  // Initialize arrays with zeros
  for (int i = 0; i < arraySize; i++) {
    sensor1Values[i] = 0;
    sensor2Values[i] = 0;
  }
}
void CPG_forword(){
    for(i=0;i<=Output;i++)
  {
    if (i == 0) {
      C1_Values[i] = C1;
      O1_Values[i] = tanh(C1_Values[i]);
      C2_Values[i] = C2;
      O2_Values[i] = tanh(C2_Values[i]);
    }
    if (i >= 1) {
      C1_Values[i] = (O1_Values[i - 1] * W11) + (O2_Values[i - 1] * W21);
      O1_Values[i] = tanh(C1_Values[i]);
      C2_Values[i] = (O2_Values[i - 1] * W22) + (O1_Values[i - 1] * W12);
      O2_Values[i] = tanh(C2_Values[i]);
    }
    //-----------------------เดินหน้า------------------------------------//
    //ขาหน้าขวา
    //ก้าวหน้า
    float Step_up_ID6 = map(O1_Values[i], MIN_O1, MAX_O1, MIN_ID6, MAX_ID6);
    float Step_forward_ID8 = map(O2_Values[i], MIN_O2, MAX_O2, MIN_ID8, MAX_ID8);
    
    //ขาหลังขวา
    //ก้าวหน้า
    float Step_up_ID7 = map(O2_Values[i], MIN_O2, MAX_O2, MIN_ID7, MAX_ID7);
    float Step_forward_ID3 = map(O1_Values[i], MIN_O1, MAX_O1, MIN_ID3, MAX_ID3);
  
    //ขาหน้าซ้าย
    //ก้าวหน้า
    float Step_up_ID1 = map(O2_Values[i], MIN_O2, MAX_O2, MIN_ID1, MAX_ID1);
    float Step_forward_ID9 = map(O1_Values[i], MIN_O1, MAX_O1, MIN_ID9, MAX_ID9);

    //ขาหลังซ้าย
    //ก้าวหน้า
    float Step_up_ID4 = map(O1_Values[i], MIN_O1, MAX_O1, MIN_ID4, MAX_ID4);
    float Step_forward_ID2 = map(O2_Values[i], MIN_O2, MAX_O2, MIN_ID2, MAX_ID2);


    //-----------------เดินหน้า--------------//
    if (!working1) {
      if (!work1) {
        sc.WritePos(6, Step_up_ID6, 0, 1500);
        sc.WritePos(7, Step_up_ID7, 0, 1500);
        sc.WritePos(8, Step_forward_ID8, 0, 1500);
        sc.WritePos(3, Step_forward_ID3, 0, 1500);
        work1 = true;
      }
      else if (work1) {
        sc.WritePos(6, Step_up_ID6, 0, 1500);
        sc.WritePos(7, Step_up_ID7, 0, 1500);
        sc.WritePos(8, Step_forward_ID8, 0, 1500);
        sc.WritePos(3, Step_forward_ID3, 0, 1500);
        working1 = true;
        doing1 = false;
      }
    } else if (working1) {
      if (!doing1) {
      sc.WritePos(4, Step_up_ID4, 0, 1500);
      sc.WritePos(1, Step_up_ID1, 0, 1500);
      sc.WritePos(2, Step_forward_ID2, 0, 1500);
      sc.WritePos(9, Step_forward_ID9, 0, 1500);
      doing1 = true;
      }
      else if (doing1) {
      sc.WritePos(4, Step_up_ID4, 0, 1500);
      sc.WritePos(1, Step_up_ID1, 0, 1500);
      sc.WritePos(2, Step_forward_ID2, 0, 1500);
      sc.WritePos(9, Step_forward_ID9, 0, 1500);
      working1 = false;
      work1 = false;
      }
    }
    delay(400);
  }
}
void CPG_backword(){
  for(i=0;i<=Output;i++)
  {
    if (i == 0) {
      C1_Values[i] = C1;
      O1_Values[i] = tanh(C1_Values[i]);
      C2_Values[i] = C2;
      O2_Values[i] = tanh(C2_Values[i]);
    }
    if (i >= 1) {
      C1_Values[i] = (O1_Values[i - 1] * W11) + (O2_Values[i - 1] * W21);
      O1_Values[i] = tanh(C1_Values[i]);
      C2_Values[i] = (O2_Values[i - 1] * W22) + (O1_Values[i - 1] * W12);
      O2_Values[i] = tanh(C2_Values[i]);
    }

    //-----------------------ถอยหลัง------------------------------------//
    //ขาหน้าขวา
    //ดันตัวไปข้างหน้า
    float Step_down_ID6 = map(O1_Values[i], MIN_O1, MAX_O1, MIN_ID6, MAX_ID6);
    float Step_backward_ID8 = map(O2_Values[i], MIN_O2, MAX_O2, MIN_ID8, MAX_ID8);

    //ขาหลังขวา
    //ดันตัวไปข้างหน้า
    float Step_down_ID7 = map(O2_Values[i], MIN_O2, MAX_O2, MAX_ID7, MIN_ID7);
    float Step_backward_ID3 = map(O1_Values[i], MIN_O1, MAX_O1, MIN_ID3,  MAX_ID3);

    //ขาหน้าซ้าย
    //ดันตัวไปข้างหน้า
    float Step_down_ID1 = map(O2_Values[i], MIN_O2, MAX_O2, MAX_ID1, MIN_ID1);
    float Step_backward_ID9 = map(O1_Values[i], MIN_O1, MAX_O1, MIN_ID9,  MAX_ID9);

    //ขาหลังซ้าย
    //ดันตัวไปข้างหน้า
    float Step_down_ID4 = map(O1_Values[i], MIN_O1, MAX_O1, MIN_ID4, MAX_ID4);
    float Step_backward_ID2 = map(O2_Values[i], MIN_O2, MAX_O2, MIN_ID2,  MAX_ID2);

  //  -----------เดินถอยหลัง------------------//
    if (!working2) {
      if (!work2) {
        sc.WritePos(6, Step_down_ID6, 0, 1500);
        sc.WritePos(7, Step_down_ID7, 0, 1500);
        sc.WritePos(8, Step_backward_ID8, 0, 1500);
        sc.WritePos(3, Step_backward_ID3, 0, 1500);
        work2 = true;
        working2 = false;
        Serial.println("1 ");
      }
      else if (work2) {
        sc.WritePos(6, Step_down_ID6, 0, 1500);
        sc.WritePos(7, Step_down_ID7, 0, 1500);
        sc.WritePos(8, Step_backward_ID8, 0, 1500);
        sc.WritePos(3, Step_backward_ID3, 0, 1500);
        working2 = true;
        doing2 = false;
        Serial.println("2 ");
      }
    } else if (working2) {
      if (!doing2) {
      sc.WritePos(4, Step_down_ID4, 0, 1500);
      sc.WritePos(1, Step_down_ID1, 0, 1500);
      sc.WritePos(2, Step_backward_ID2, 0, 1500);
      sc.WritePos(9, Step_backward_ID9, 0, 1500);
      Serial.println("3");
      doing2 = true;
      working2 = true;
      }
      else if (doing2) {
      sc.WritePos(4, Step_down_ID4, 0, 1500);
      sc.WritePos(1, Step_down_ID1, 0, 1500);
      sc.WritePos(2, Step_backward_ID2, 0, 1500);
      sc.WritePos(9, Step_backward_ID9, 0, 1500);
      Serial.println("4 ");
      working2 = false;
      work2 = false;
      }
    }
    delay(400);
  }
}

void voice1(){
  if (isBeeping) {
    unsigned long currentMillis2 = millis();
    // Check if the beep duration has passed
      tone(buzzerPin, beepFrequency);
      beepCompleted = true;
      Serial.println("voice 1");
      isBeeping = false;
  }
     else{
      // Stop the beep
      noTone(buzzerPin);
      beepCompleted = true;
      Serial.println("stop voice 1");
      isBeeping = true;
    }
}

void voice2(){
  if (isBeeping) {
    unsigned long currentMillis2 = millis();
    // Check if the beep duration has passed
    if (currentMillis2 - startMillis2 >= beepDuration) {
      tone(buzzerPin, beepFrequency2);
      beepCompleted = true;
      Serial.println("voice 2");
      isBeeping = false;
    }
  }else{
      noTone(buzzerPin);
      beepCompleted = true;
      Serial.println("stop voice 2");
      isBeeping = true;
  }
}

void novoice(){
  if (isBeeping) {
    unsigned long currentMillis2 = millis();
    // Check if the beep duration has passed
    if (currentMillis2 - startMillis2 >= beepDuration) {
      // Stop the beep
      noTone(buzzerPin);
      beepCompleted = true;
      Serial.println("no voice");
      isBeeping = false;
    }
  }else{
      // Stop the beep
      noTone(buzzerPin);
      beepCompleted = true;
      Serial.println("stop no voice");
      isBeeping = true;
  }
}


void loop() {
  unsigned long currentMillis = millis();
  if (currentMillis - previousMillis >= interval) {
    previousMillis = currentMillis;

    // Sensor 1
    digitalWrite(trigPin1, LOW);
    delayMicroseconds(5);
    digitalWrite(trigPin1, HIGH);
    delayMicroseconds(10);
    digitalWrite(trigPin1, LOW);
    duration1 = pulseIn(echoPin1, HIGH);
    cm1 = (duration1 / 2) / 29.1;

    // Sensor 2
    digitalWrite(trigPin2, LOW);
    delayMicroseconds(5);
    digitalWrite(trigPin2, HIGH);
    delayMicroseconds(10);
    digitalWrite(trigPin2, LOW);
    duration2 = pulseIn(echoPin2, HIGH);
    cm2 = (duration2 / 2) / 29.1;

    // Map sensor 1 value in cm
    int mappedCm1;
    if (cm1 >= 20 && cm1 <= 40) {
      mappedCm1 = map(cm1, 20, 40, 10, 0);
    } else if (cm1 > 40) {
      mappedCm1 = 0;
    } else {
      mappedCm1 = 10;  // Set to 10 for values less than 20
    }

    // Map sensor 2 value in cm
    int mappedCm2;
    if (cm2 >= 20 && cm2 <= 40) {
      mappedCm2 = map(cm2, 20, 40, 10, 0);
    } else if (cm2 > 40) {
      mappedCm2 = 0;
    } else {
      mappedCm2 = 10;  // Set to 10 for values less than 20
    }

    // Store the mapped values in the arrays
    sensor1Values[index] = mappedCm1;
    sensor2Values[index] = mappedCm2;
   

    // Update the index, wrap around if necessary
    index = (index + 1) % arraySize;

    // Print the current values of the arrays
    // Serial.print("    Sensor 1 values: ");
    for (int i = 0; i < arraySize; i++) {
      // Serial.print(sensor1Values[i]);
      if (i < arraySize - 1) {
        // Serial.print(", ");
      }
    }
    // Print the current values of the arrays
    // Serial.print("    Sensor 2 values: ");
    for (int i = 0; i < arraySize; i++) {
      // Serial.print(sensor2Values[i]);
      if (i < arraySize - 1) {
        // Serial.print(", ");
      }
    }

     // Calculate the standard deviations
    float mean1 = 0;
    float mean2 = 0;

    ///---------- ผลรวมตัวเลข ----------///
    for (int i = 0; i < arraySize; i++) {
      mean1 += sensor1Values[i];
      mean2 += sensor2Values[i];
    }

    ///---------- ค่าเฉลี่ย ----------///
    mean1 /= arraySize;
    mean2 /= arraySize;

    float variance1 = 0;
    float variance2 = 0;

    ///---------- ผลรวม (Xi - X(เฉลี่ย)) ยกกำลัง 2 ----------///
    for (int i = 0; i < arraySize; i++) {
      variance1 += pow(sensor1Values[i] -mean1, 2);
      variance2 += pow(sensor2Values[i] - mean2, 2);
    }

   ///---------- ผลรวม (Xi - X(เฉลี่ย)) ยกกำลัง 2 หาร n-1  ----------///
    variance1 /= arraySize-1;
    variance2 /= arraySize-1;

///----------- ถอดสเเควรูท = ส่วนเบี่ยงเบนมาตรฐาน ----------------//
    float stddev1 = sqrt(variance1);
    float stddev2 = sqrt(variance2);

    // Store standard deviations in variables x1 and x2
    float x1 = stddev1;
    float x2 = stddev2;

    // Exponential calculations
    float e = 2.71828;
    float a = 0.7;
    float b = 0.25;
    int TH = 5;

    // ----- Store Map sensor 1 to Sensor1 , Store Map sensor 1 to Sensor1 -------/
    int Sensor1 = mappedCm1;
    int Sensor2 = mappedCm2;

    ///--------- e ยกกำลัง ของ Hc1 Hc2 --------------//
    float reX1 = pow(e, ((-1)*(x1)));
    float reX2 = pow(e, ((-1)*(x2)));

    // Calculate firstx1 and secx1 for Hc1
    float firstx1 = a * (1 / (1 + reX1));
    float secx1 = b * Hc1[0];  

    // Calculate firstx2 and secx2 for Hc2 
    float firstx2 = a * (1 /(1 + reX2));
    float secx2 = b * Hc2[0];
  
    // Add firstx1 and secx1 for store in Hc1[1] 
    Hc1[1] = firstx1 + secx1;

    // Add firstx2 and secx2 for store in Hc2[1]
    Hc2[1] = firstx2 + secx2;

    // Map Hc1[1] to R_Hc1
    float R_Hc1 = (Hc1[1] * 2.0f) - 1.0f;
    float R_Hc2 = (Hc2[1] * 2.0f) - 1.0f;

    /// strt area for loop hormones //

  if (Sensor1 < (TH - R_Hc1) && Sensor2 < (TH - R_Hc2)) {
      novoice();
      CPG_forword();
      // CPG_forward();
      Serial.print(Hc1[0]);
      Serial.print(", ");
      Serial.print(Hc1[1]);
      Serial.print("  R_HC1 = ");
      Serial.print(R_Hc1);
      Serial.print("  ");
      Serial.print(Hc2[0]);
      Serial.print(", ");
      Serial.print(Hc2[1]);
      Serial.print("  R_HC2 = ");
      Serial.print(R_Hc2);
      Serial.print("  Sensor 1 = ");
      Serial.print(Sensor1);
      Serial.print("  Sensor 2 = ");
      Serial.print(Sensor2);
      Serial.print("  ");
      Serial.print("    Normal + forward");
      Serial.print("\n");

    
    } 
    else if (Sensor1 > (TH - R_Hc1) && Sensor2 < (TH - R_Hc2)) {
      voice1();
      CPG_backword();
      // CPG_Backward();
      Serial.print(Hc1[0]);
      Serial.print(", ");
      Serial.print(Hc1[1]);
      Serial.print("  R_HC1 = ");
      Serial.print(R_Hc1);
      Serial.print("  ");
      Serial.print(Hc2[0]);
      Serial.print(", ");
      Serial.print(Hc2[1]);
      Serial.print("  R_HC2 = ");
      Serial.print(R_Hc2);
      Serial.print("  Sensor 1 = ");
      Serial.print(Sensor1);
      Serial.print("  Sensor 2 = ");
      Serial.print(Sensor2);
      Serial.print("  ");
      Serial.print("      Back + voice1");
      Serial.print("\n");

    } 
    else if (Sensor1 < (TH - R_Hc1) && Sensor2 > (TH - R_Hc2)) {
      // voice2();
      voice1();
      CPG_forword();
      Serial.print(Hc1[0]);
      Serial.print(", ");
      Serial.print(Hc1[1]);
      Serial.print("  R_HC1 = ");
      Serial.print(R_Hc1);
      Serial.print("  ");
      Serial.print(Hc2[0]);
      Serial.print(", ");
      Serial.print(Hc2[1]);
      Serial.print("  R_HC2 = ");
      Serial.print(R_Hc2);
      Serial.print("  Sensor 1 = ");
      Serial.print(Sensor1);
      Serial.print("  Sensor 2 = ");
      Serial.print(Sensor2);
      Serial.print("  ");
      Serial.print("      forward + voice1");
      Serial.print("\n");
    } 
    else if (Sensor1 > (TH - R_Hc1) && Sensor2 > (TH - R_Hc2)) {
      voice2();
      // CPG_backword();
      Serial.print(Hc1[0]);
      Serial.print(", ");
      Serial.print(Hc1[1]);
      Serial.print("  R_HC1 = ");
      Serial.print(R_Hc1);
      Serial.print("  ");
      Serial.print(Hc2[0]);
      Serial.print(", ");
      Serial.print(Hc2[1]);
      Serial.print("  R_HC2 = ");
      Serial.print(R_Hc2);
      Serial.print("  Sensor 1 = ");
      Serial.print(Sensor1);
      Serial.print("  Sensor 2 = ");
      Serial.print(Sensor2);
      Serial.print("  ");
      Serial.print("      Stop + voice2");
      Serial.print("\n");
    } 

    /// end area for loop hormones //


/// ---------- print test Hc1 ---------------------//
    // Serial.print("   Standard Deviation Sensor 1: ");
    // Serial.print(x1);
    // Serial.print("  ");
    // Serial.print(reX1);
    // Serial.print("  ");
    // // Serial.print("  mean 1: ");
    // Serial.print(firstx1);
    // Serial.print(" + ");
    // Serial.print(secx1);
    // Serial.print(" = ");
    // // Serial.print("  ");
    // Serial.print(Hc1[1]);
    // Serial.print(" Hc1  =  ");
    // Serial.print(Hc1[0]);
    // Serial.print(", ");
    // Serial.print(Hc1[1]);
    // Serial.print("  R_HC1 = ");
    // Serial.println(R_Hc1);
    
    // Serial.println("  ");

    /// ---------- print test Hc2 ---------------------//
    // Serial.print("   Standard Deviation Sensor 2: ");
    // Serial.print(x2);
    // Serial.print("  ");
    // Serial.print(reX2);
    // Serial.print("  ");
    // // Serial.print("  mean 2: ");
    // Serial.print(firstx2);
    // Serial.print(" + ");
    // Serial.print(secx2);
    // Serial.print(" = ");
    // // Serial.print("  ");
    // Serial.print(Hc2[1]);
    // Serial.print("  ");
    // Serial.print(Hc2[0]);
    // Serial.print(", ");
    // Serial.print(Hc2[1]);
    // Serial.println("  ");

    // Update Hc1[0] for the next iteration
    Hc1[0] = Hc1[1];
    Hc2[0] = Hc2[1];
    
    //---------------- cheack S.D ------------------------///
    // Serial.print("  mean 1: ");
    // Serial.print(mean1);
    // Serial.print("  varoance 1: ");
    // Serial.print(variance1);
    // Print the standard deviations and number of valid entries for debugging purposes
    // Serial.print("   Standard Deviation Sensor 1: ");
    // Serial.println(x1);
    // Serial.print("  mean 2: ");
    // Serial.print(mean2);
    // Serial.print("  varoance 2: ");
    // Serial.print(variance2);
    // Serial.print("    Standard Deviation Sensor 2: ");
    // Serial.println(x2);
    // Serial.print("Number of valid entries in sensor1Values: ");
    // Serial.println(validEntries);

    //---------------- cheack S.D ------------------------///
  }

}
